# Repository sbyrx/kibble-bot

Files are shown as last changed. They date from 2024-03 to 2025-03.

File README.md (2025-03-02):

# KibbleBot
A 3D printed kibble/treat dispenser powered by an Arduino Nano ESP32 or a Raspberry Pi Pico W. Give your pet a treat even if you're not home!

**Update 2025-03-01:**
Added Arduino support and instructions for controlling KibbleBot via Arduino Cloud.

**Update 2024-04-10:**
Added a new version of the model which allows KibbleBot to be mounted to a wall and the hopper is now attached more securely using screws.

## Features
- Kibbles dispensed through the push of a button or remotely through a web app (Pi Pico) or Arduino Cloud (Nano ESP32)
- Easy to print and build
- Minimal electronics
- Happy puppers

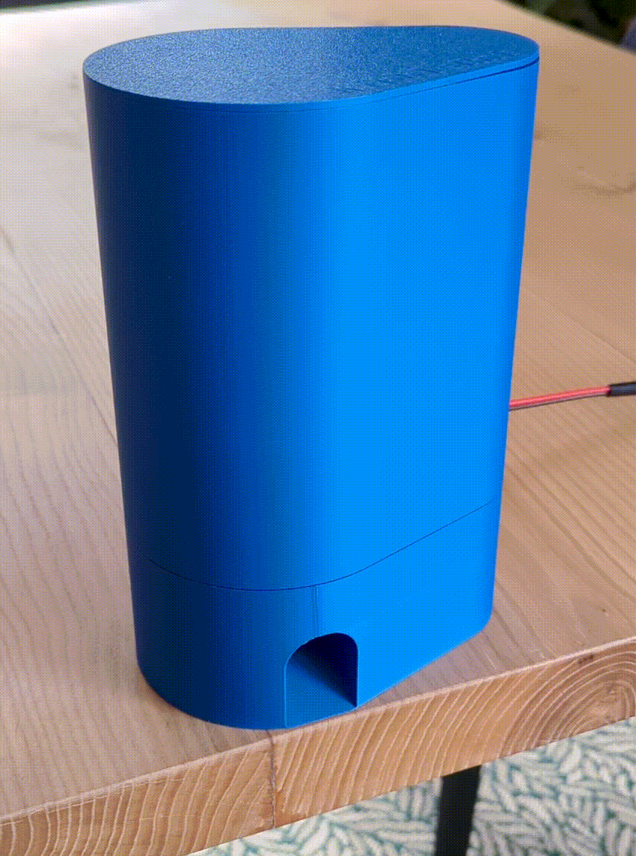
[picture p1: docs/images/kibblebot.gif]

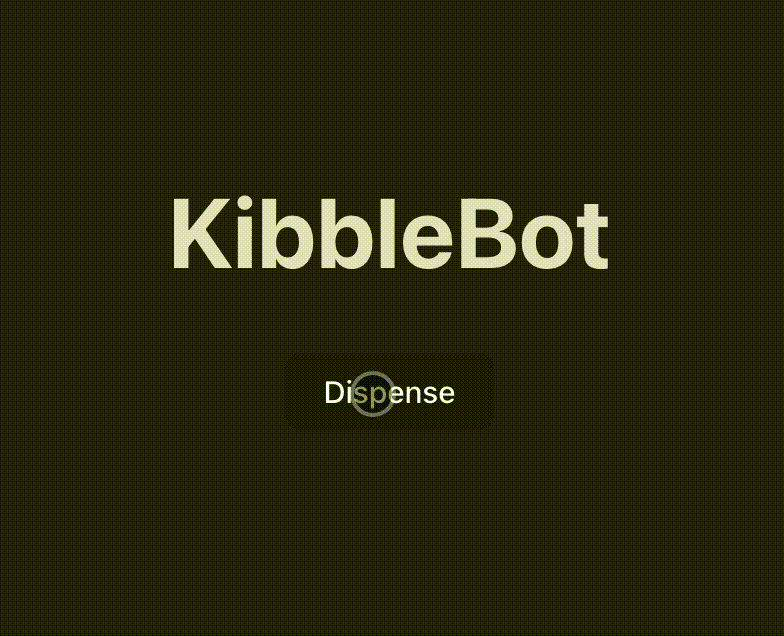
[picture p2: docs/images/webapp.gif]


## Build Instructions
### Parts List
Before you get started, here are all the things you'll need to buy to build your very own KibbleBot. For reference I've included links to the products I purchased:
1. [Arduino Nano ESP 32](https://store.arduino.cc/products/nano-esp32)
1. OR Raspberry Pi Pico W
    - Source from your local [Raspberry Pi authorized reseller](https://www.raspberrypi.com/resellers/)
1. [Easy Driver Stepper Motor Controller](https://ca.robotshop.com/products/easydriver-stepper-motor-controller-a3967)
1. [NEMA 17 Stepper Motor (12V and 350mA)](https://www.pishop.ca/product/stepper-motor-nema-17-size-200-stepsrev-12v-350ma/)
1. 12V Power Supply (I use one I had laying around)
1. [M2x5mm Screws](https://www.amazon.ca/dp/B0C38YFL3D)
1. [M3x6mm Screws](https://www.amazon.ca/dp/B0C38YFL3D)
1. [M3 Flat Washer](https://www.amazon.ca/dp/B0C38YFL3D)
1. [M2x4mm Heat Set Nuts (3.2mm outer diameter)](https://www.amazon.ca/dp/B0CNRSJ1B2)
1. [M3x4mm Heat Set Nuts (4.2mm outer diameter)](https://www.amazon.ca/dp/B0CNRSJ1B2)
1. [6x6x4.3mm TACT Switch Push Button](https://www.amazon.ca/dp/B06Y6DDG8K)
1. [12V DC Barrel Connector (11mm outer diameter)](https://www.amazon.ca/dp/B08SJM2G52)
1. Solder and wire
1. Heat shrink tube
1. [Heat sinks](https://www.amazon.ca/dp/B0814V66JV) (optional, but the Easy Driver can get pretty hot)

### 3D Printed Parts
Print all parts with 0.2mm layer height and 15% infill. I recommend printing both gears with 4 wall loops for some added strength.

I've included [Bambu Studio Project file](docs/models/kibble_bot.3mf) with all parts laid out on two build plates and configured.

|Model|Image|Details|
|-----|-----|---|
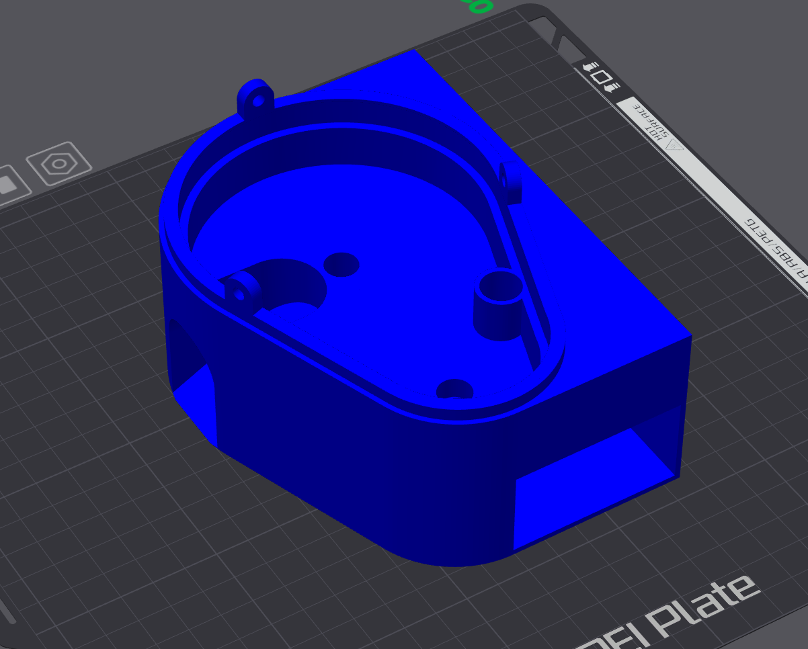
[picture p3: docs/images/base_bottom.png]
Rendering of the Base Bottom
|[Base Bottom](docs/models/base_bottom.stl)||Base of the KibbleBot which the Base Top and Hopper rest on. It has two holes for each gear to rest in and a third for running the stepper motor wire through. It also contains the chute that kibbles come out of and the cut out for the electronics drawer on the side. Can be wall mounted using the holes on the back.<br><br>**Print Orientation**: Right side up<br>**Quantity**: 1<br>**Supports**: Yes|
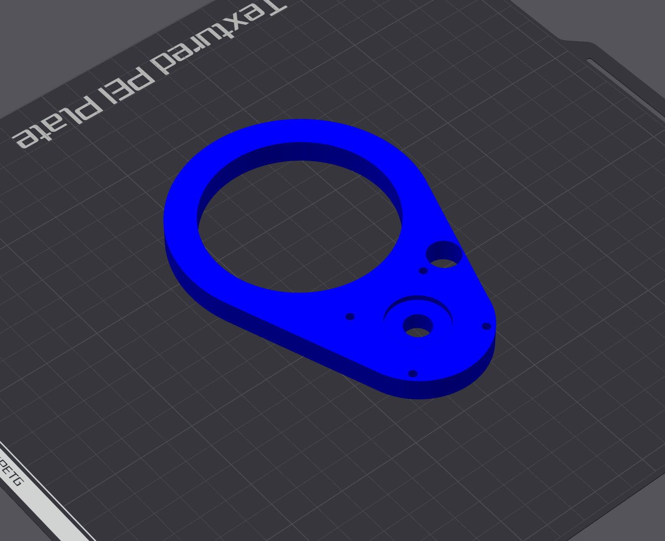
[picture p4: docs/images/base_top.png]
Rendering of the Base Top
|[Base Top](docs/models/base_top.stl)||The Base Top sits inside the Base Bottom covering both gears. It has mounting holes in a 31mm pattern to mount the NEMA 17 stepper motor. You may need to drill out the holes with a small drill bit in order to fit the screws in.<br><br>**Print Orientation**: Side up down<br>**Quantity**: 1<br>**Supports**: No|
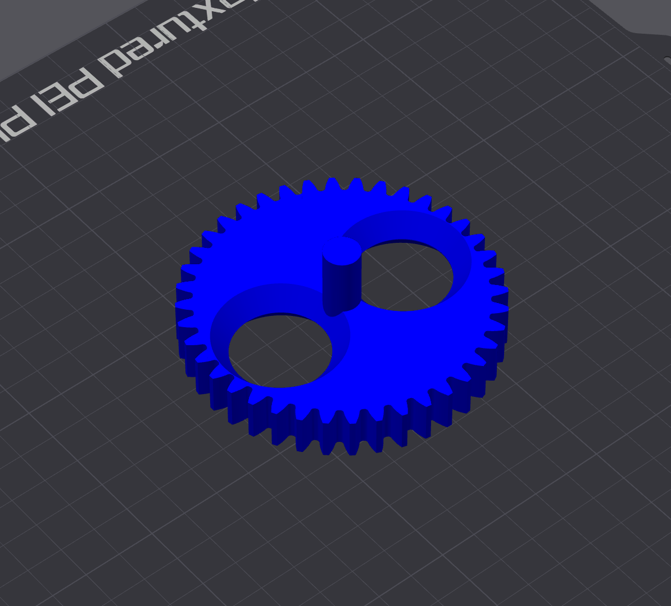
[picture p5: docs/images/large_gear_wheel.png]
Rendering of the Large Gear Wheel
|[Large Gear Wheel](docs/models/large_gear_wheel.stl)||The Large Gear Wheel is spun 180 degrees by the Small Gear Wheel allowing kibbles to fall through it and down the chute in the base bottom. It also has two holes for the optional Stir Sticks if you find that kibbles are getting stuck in the Hopper.<br><br>**Print Orientation**: Side up down<br>**Quantity**: 1<br>**Supports**: No|
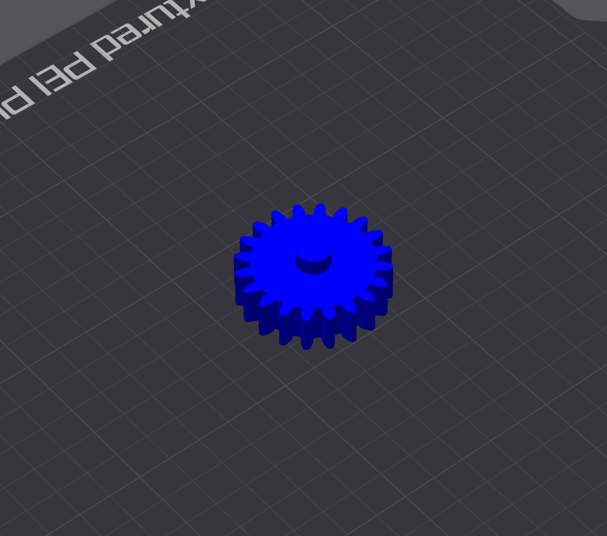
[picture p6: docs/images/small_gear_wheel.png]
Rendering of the Small Gear Wheel
|[Small Gear Wheel](docs/models/small_gear_wheel.stl)||The Small Gear Wheel is connected to the stepper motor and turns the Large Gear Wheel.<br><br>**Print Orientation**: Side up down<br>**Quantity**: 1<br>**Supports**: No|
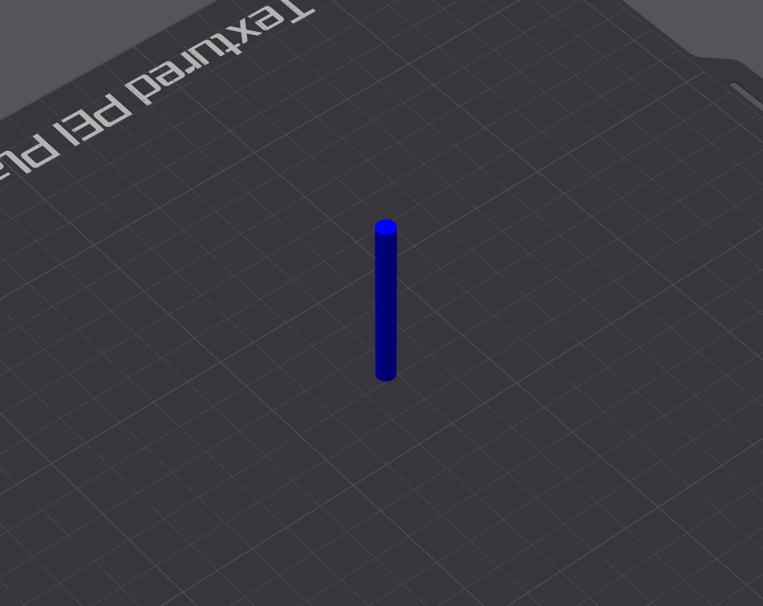
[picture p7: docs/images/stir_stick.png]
Rendering of the Stir Stick
|[Stir Stick](docs/models/stir_stick.stl) (optional)||Slots into the top of the Large Gear Wheel and can help with kibbles getting stuck in the Hopper and not flowing through.<br><br>**Print Orientation**: Vertical<br>**Quantity**: 2<br>**Supports**: Yes (brim)|
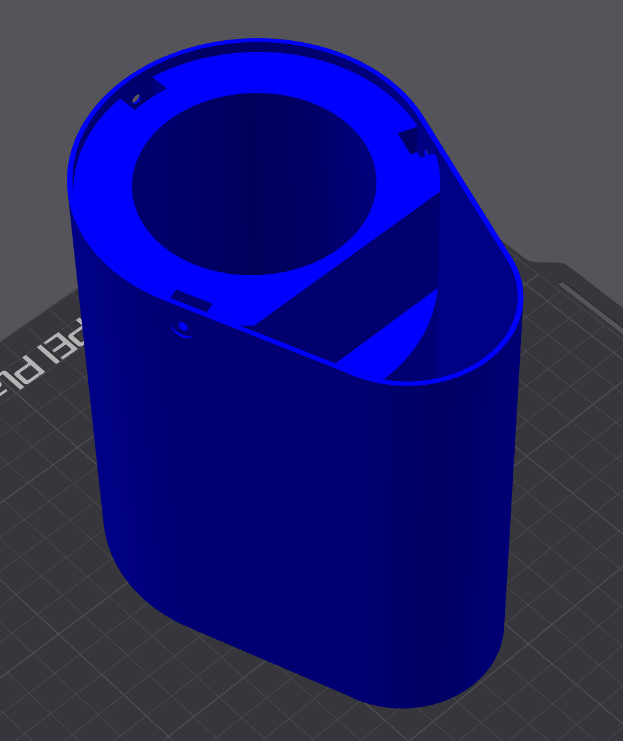
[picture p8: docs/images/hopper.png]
Rendering of the Hopper
|[Hopper](docs/models/hopper.stl)||The Hopper sits on top of the Base Bottom and holds kibbles to be dispensed. Contains a cut out so that it will fit over the stepper motor.<br><br>**Print Orientation**: Up side down<br>**Quantity**: 1<br>**Supports**: No|
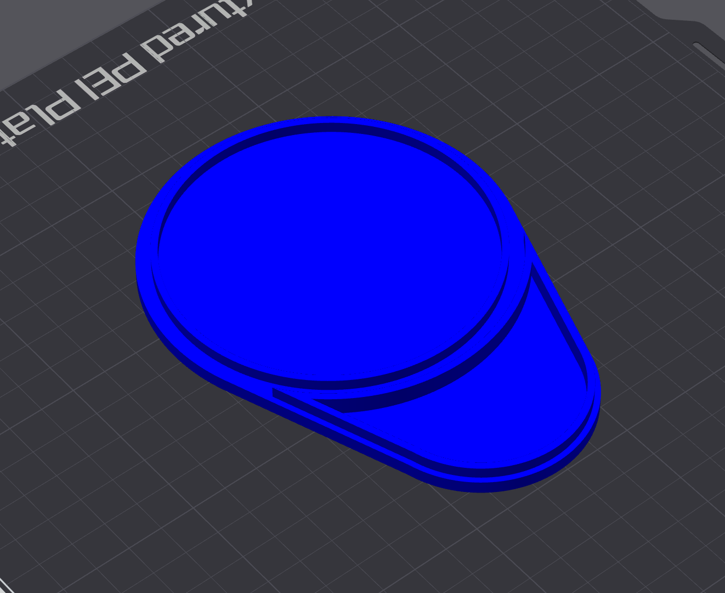
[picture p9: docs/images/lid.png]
Rendering of the Lid
|[Lid](docs/models/lid.stl)||Sits on top of the Hopper to close it off.<br><br>**Print Orientation**: Up side down<br>**Quantity**: 1<br>**Supports**: No|
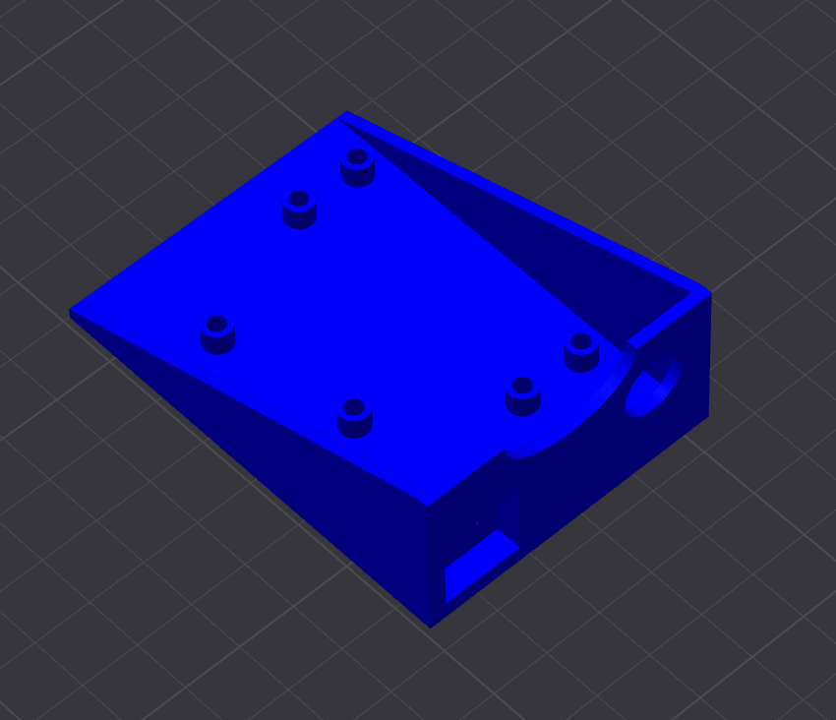
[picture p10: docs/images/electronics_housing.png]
Rendering of the Electronics Housing
|[Electronics Housing](docs/models/electronics_housing.stl)||Houses the Raspberry Pi Pico and the Easy Driver with four holes for the M2 heat set nuts to mount both boards. Also has cut outs for the barrel connector to pass through and to mount the button.<br><br>**Print Orientation**: Right side up<br>**Quantity**: 1<br>**Supports**: Yes|
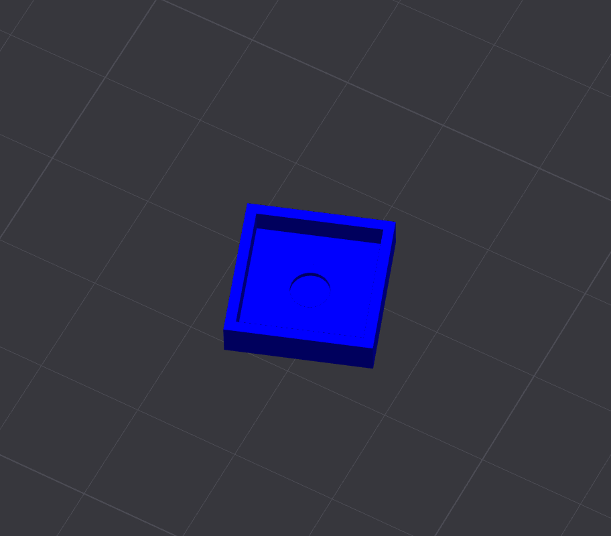
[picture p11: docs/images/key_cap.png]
Rendering of the Key Cap
|[Key Cap](docs/models/key_cap.stl)||The Key Cap is glued on top of the TACT Button and fits inside of a recessed compartment in the Electronics Housing.<br><br>**Print Orientation**: Up side down<br>**Quantity**: 1<br>**Supports**: No|
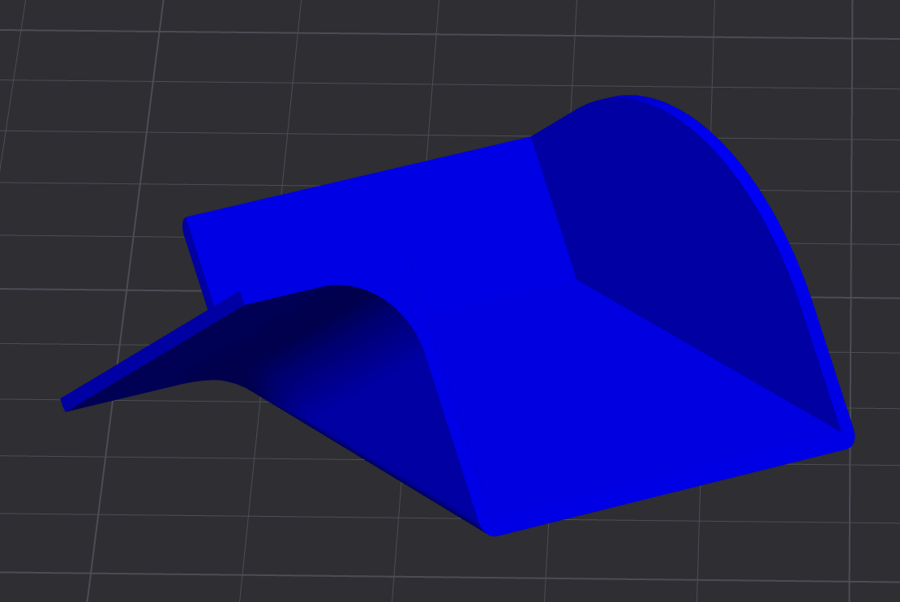
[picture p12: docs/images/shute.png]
Rendering of the Shute
|[Shute (optional)](docs/models/shute.stl)||Redirects the kibbles off to the left instead of straight down.<br><br>**Print Orientation**: Flat side<br>**Quantity**: 1<br>**Supports**: Yes|

### Assembly
Begin by setting the M3 heat set nuts into the three tabs in the Base Bottom which will hold the hopper in place.

Mount the stepper motor to the Base Top. Pass the ribbon cable through the holes in the Base Top and Base Bottom into the electronics drawer.

Then, assemble the rest of the 3D printed parts like so:

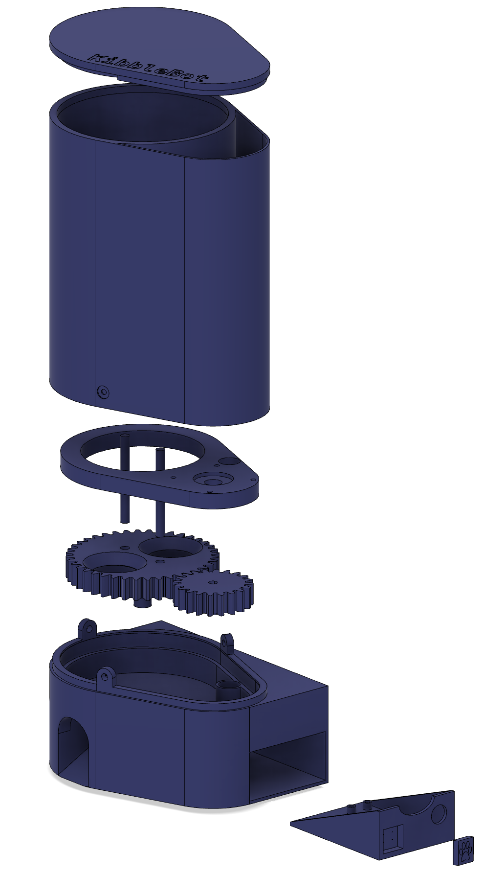
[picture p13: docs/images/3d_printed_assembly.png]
KibbleBot Exploded View


Screw three M3x6mm screws with flat washers through the holes in the Hopper to securely attach it to the Base Bottom.

## Electronics
Below I've provided instructions for two different options for adding smarts to your KibbleBot, either an Arduino Nano ESP32 using Arduino Cloud (easy) or an Raspberry Pi Pico W with a simple web server (a bit more complicated).

### Arduino Nano ESP32
#### Wiring
Since the Nano uses 3.3V logic, the first thing you should do is switch the Easy Driver to use 3.3V logic as well by soldering SJ2 closed (placing a small glob of solder on the two pads on the bottom left hand corner of the board where it's written "5V/3V"). You can confirm you've done this correctly by measuring the voltage across the +5V Output and GND, which should now be 3.3V.

Next, wire the Easy Driver to the Nano as follows:
1. DIR -> D2
1. STEP -> D3
1. SLP -> D4
1. GND -> GND

Connect one side of the TACT Button to D5 and the other side to ground. I used a little bit of CA glue on the back of the button to glue it to the electronics housing, as well as some glue on the back of the keycap to glue it to the TACT Button.

The Easy Driver has a 5V (3.3V) output which can be used to power the Nano. Wire the 5V (now 3.3V) output on the Easy Driver to VIN on the Nano and GND to GND. The Nano's VIN pin can accept an input voltage range of 6-21V, so you could also power it directly from the 12V power supply.

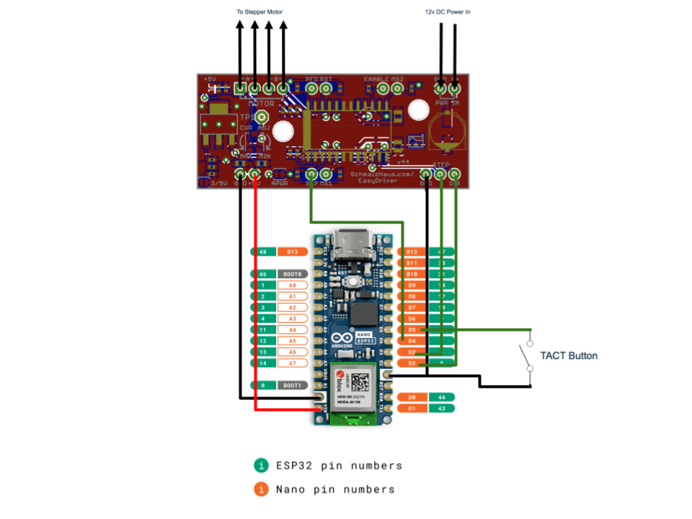
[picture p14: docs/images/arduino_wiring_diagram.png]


Set the heat set nuts into their holes in the bottom of the housing, and mount both boards using the M2 screws.

Plug in your stepper motor, connect your 12V power supply to PWR IN on the Easy Driver, and you should be all set with the electronics!

#### Code
Begin by following [the instructions](https://docs.arduino.cc/tutorials/nano-esp32/cloud-setup/) on the Arduino website for configuring your Nano ESP32, connecting it to your WiFi, and hooking it up to the Arduino Cloud, and creating a new "Thing".

Once completed, on the Setup tab of your Thing, add a new Read/Write variable called `dispense` of type `boolean`. 

Now select the Sketch tab. The Arduino Cloud IDE will have auto-generated a sketch with some boilerplate code for connecting to WiFi and to the cloud as well as a function called `onDispenseChange()` which will be triggered anytime our `boolean` variable is changed.

Open up `kibblebot.ino` and copy the contents of it into your sketch in the Arduino Cloud. Compile the sketch and upload it to the Nano.

The last step is to create a [Dashboard](https://app.arduino.cc/dashboards) which will tell the Nano to dispense kibbles when a button is pressed. Create a new Dashboard, click the Edit button, then Add, and choose the Button type. Link it to your `dispense` variable and give it a name.

When the button is pressed, `onDispenseChange()` will be called in your sketch via the Arduino Cloud, and kibbles will be dispensed!

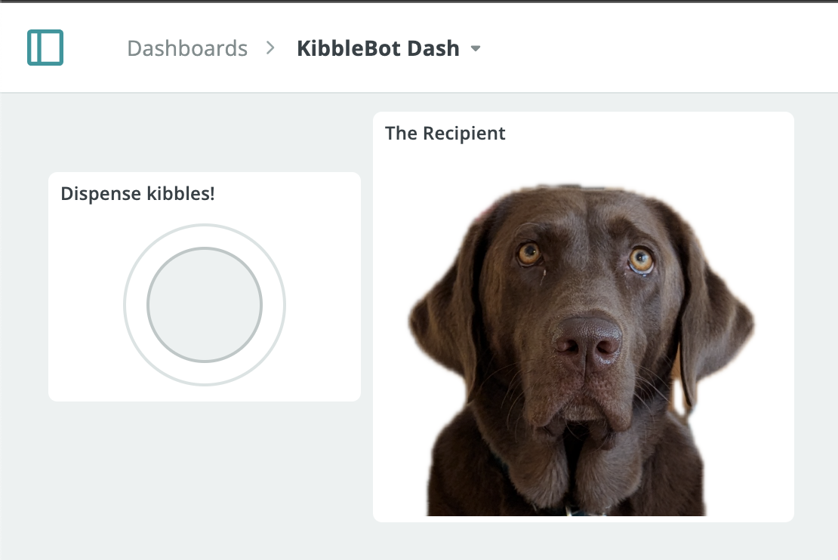
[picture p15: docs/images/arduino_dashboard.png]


### Raspberry Pi Pico
#### Wiring
Since the Pico uses 3.3V logic, the first thing you should do is switch the Easy Driver to use 3.3V logic as well by soldering SJ2 closed (placing a small glob of solder on the two pads on the bottom left hand corner of the board where it's written "5V/3V"). You can confirm you've done this correctly by measuring the voltage across the +5V Output and GND, which should now be 3.3V.

Next, wire the Easy Driver to the Pico as follows:
1. DIR -> GP15
1. STEP -> GP14
1. GND -> GND (Pin 18)
1. SLP -> GP13 

Connect one side of the TACT Button to GP10 and the other to ground (Pin 13). I used a little bit of CA glue on the back of the button to glue it to the electronics housing, as well as some glue on the back of the keycap to glue it to the TACT Button.
+
The Easy Driver has a 5V (3.3V) output which I'm taking advantage of to power the Pico. Wire the 5V (now 3.3V) output on the Easy Driver to VSYS on the Pico, and GND to GND.

Set the heat set nuts into their holes in the bottom of the housing, and mount both boards using the M2 screws.

Plug in your stepper motor, connect your 12V power supply to PWR IN on the Easy Driver, and you should be all set with the electronics!

**Note:** I've opted to solder headers to each board and make the connections using jumper wires. That being said, it's important to make sure the PWR IN and stepper motor connections are solid or you risk blowing up the Easy Driver. Always power off the Easy Driver before plugging/unplugging the stepper motor!

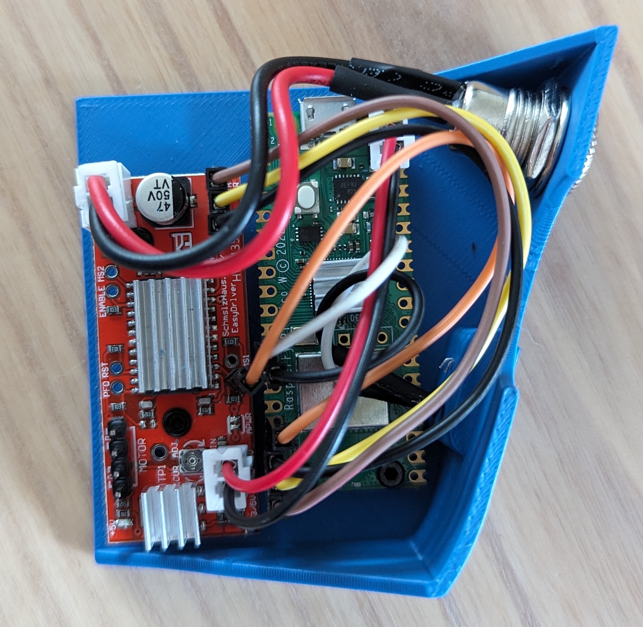
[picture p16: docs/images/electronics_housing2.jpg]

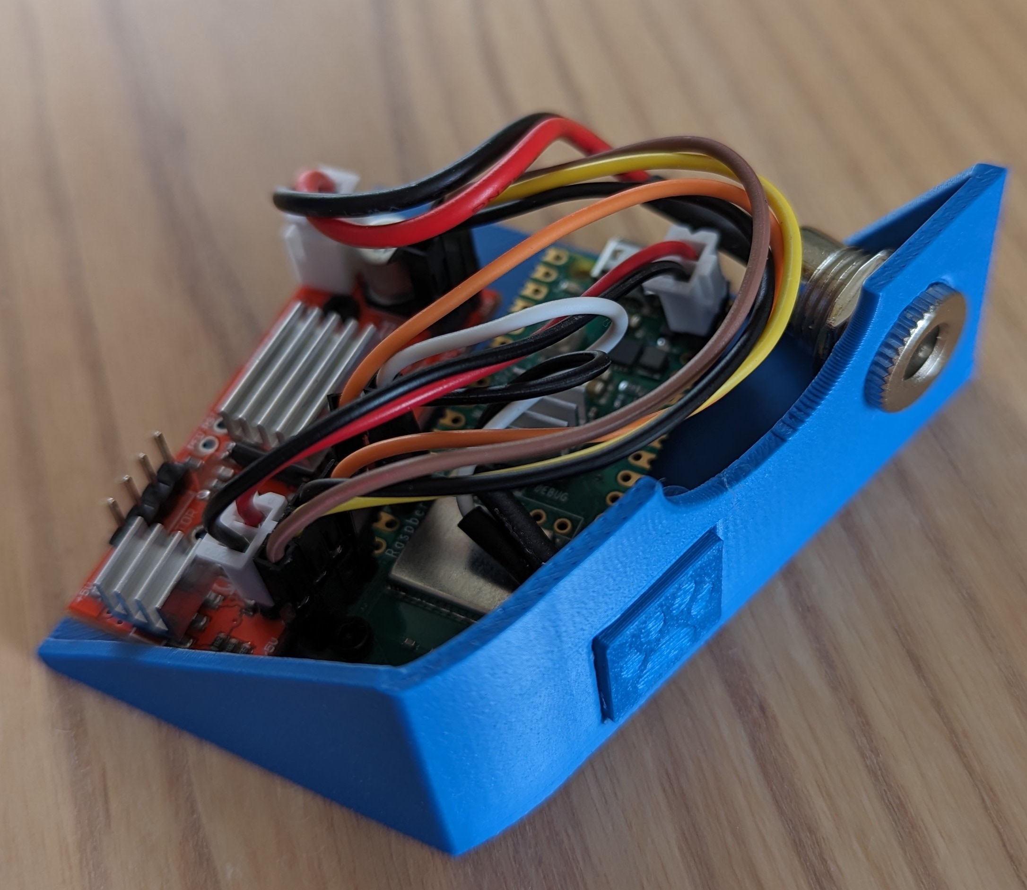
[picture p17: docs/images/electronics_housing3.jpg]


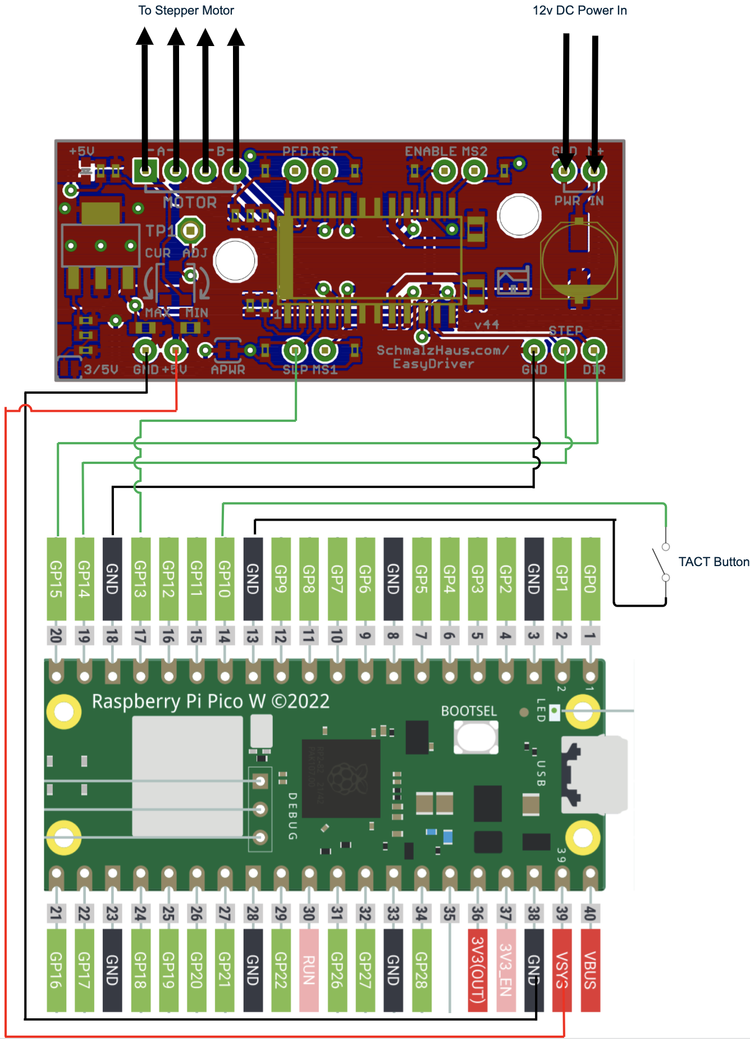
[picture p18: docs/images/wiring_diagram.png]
KibbleBot wiring diagram


#### Code

The KibbleBot software for the Pico is written in Micropython. Follow the [instructions here](https://www.raspberrypi.com/documentation/microcontrollers/micropython.html) to flash Micropython onto your board.

I also recommend setting up a Visual Studio project and installing the [MicroPico extension](https://github.com/paulober/MicroPico) to copy the code to the board.

You'll also need to have `NodeJS` and `npm` set up on your machine in order to build the web app.

##### main.py

This is the Micropython code which runs on the Pico and interfaces with the Easy Driver to turn the stepper motor and dispense kibbles. It first connects to WiFi and then listens for button presses and has a simple web server to listen for web requests.

To run the code on your Pico, first edit `main.py` and set the WiFi SSID and password. Then connect your Pico to your computer, and wait for VSCode to show "Pico Connected" in the bottom toolbar. Then right click on `main.py` and click "Upload current file to Pico".

##### Web App

I've created a simple Svelte app which `main.py` serves up and allows kibbles to be dispensed from a web browser. The web app is built into a single HTML file to make it easy for the Micropython code to serve up.

You'll need to build the web application and copy the resulting `index.html` to the Pico:
1. Open up a terminal and set the working directory to `/web`
1. Run `npm install`
1. Run `npm run build`
1. Open the resulting `/web/dist/index.html` file
1. Right click on it and click "Upload current file to Pico"

In VSCode, click "Toggle Pico-W-FS" in the bottom toolbar. The "Pico (W) Remote Workspace" view should now show two files: `main.py` and `index.html`.

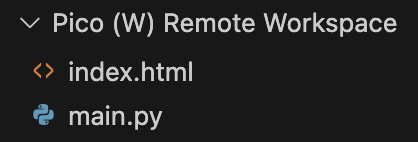
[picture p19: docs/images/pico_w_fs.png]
Screenshot of the Pico W FS view


With both files copied to your Pico, you're good to go! Unplug it from your computer and power everything up with the 12V supply. When the Pico shows a solid green LED it means it's connected to WiFi and ready to go. Navigate to the Pico's IP address in your browser and click "Dispense"!

#### Accessing KibbleBot remotely

If your home router supports running a VPN server, this is likely your easiest option for accessing the KibbleBot when not at home. Simply connect your phone/laptop to the VPN and browse to the local IP address of the Pico.

Another option is a [Cloudflare Zero-Trust tunnel](https://www.cloudflare.com/products/tunnel/), but this requires you to run the Cloudflare client on another machine that's always powered on.

In my set up I've opted to use a Cloudflare tunnel as I already have the Cloudflare client running on my home server and several tunnels configured. This set up enables me to share the URL with friends and family so they can dispense kibbles too. I've included the Micropython code that I use (`main_rate_limiting.py`) which keeps track of the number of kibbles each user has dispensed and limits them to once per week.

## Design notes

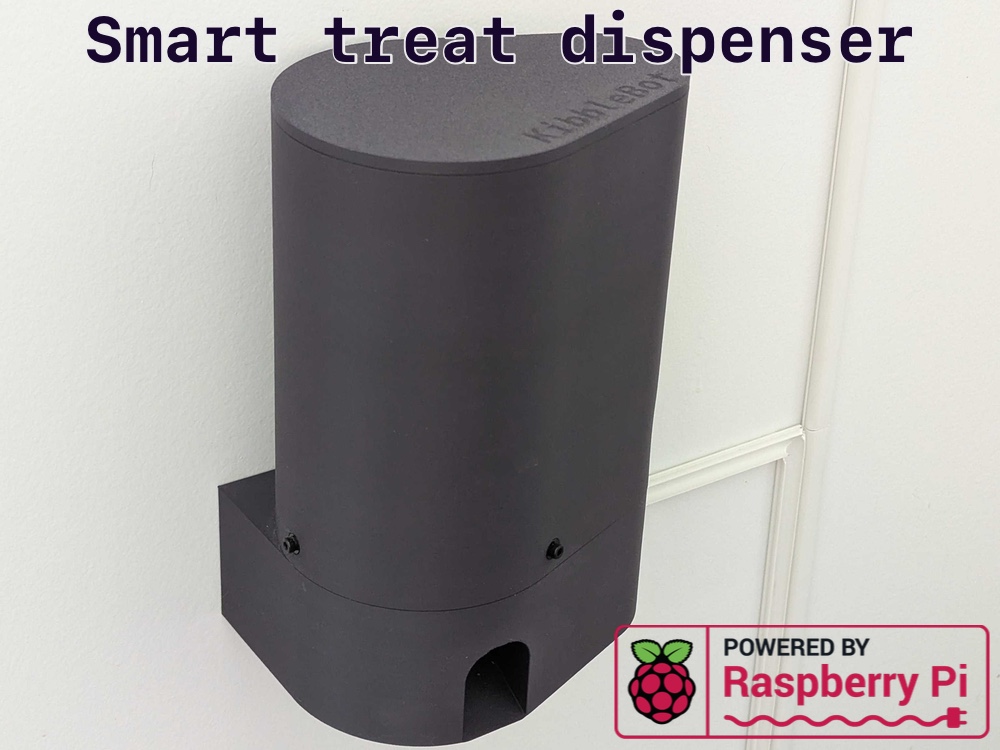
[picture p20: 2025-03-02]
docs/images/thumbnail-pico.jpeg

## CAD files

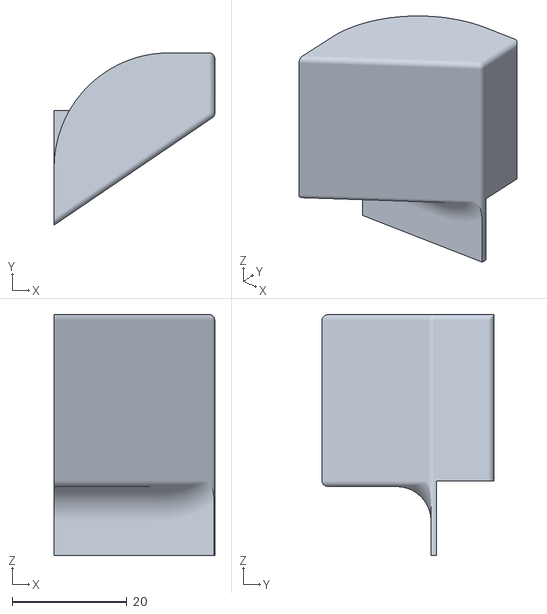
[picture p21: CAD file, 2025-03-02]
docs/models/shute.stl
28.0 x 30.0 x 42.0

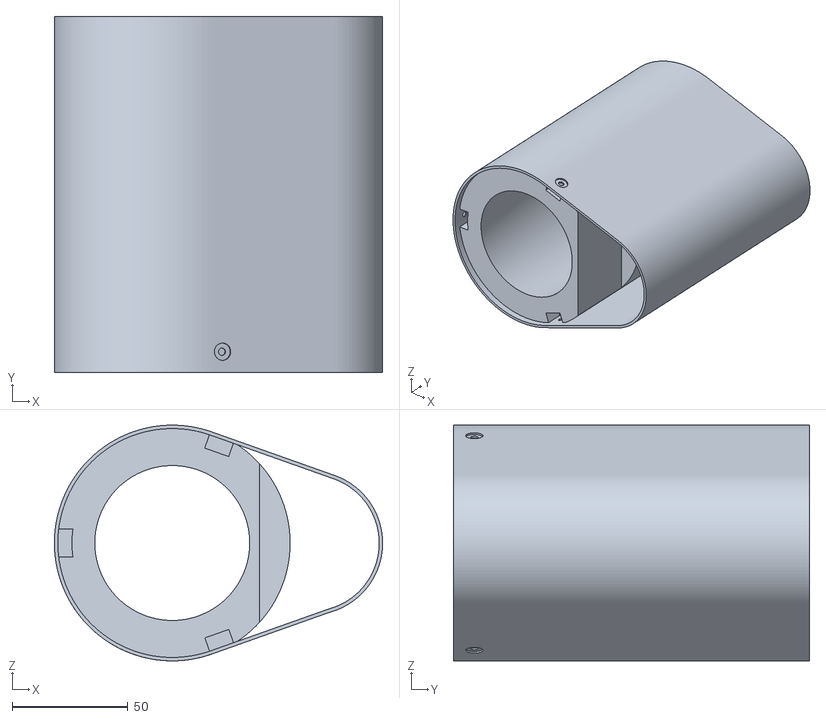
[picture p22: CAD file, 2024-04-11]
docs/models/hopper.stl
142.0 x 154.0 x 102.0

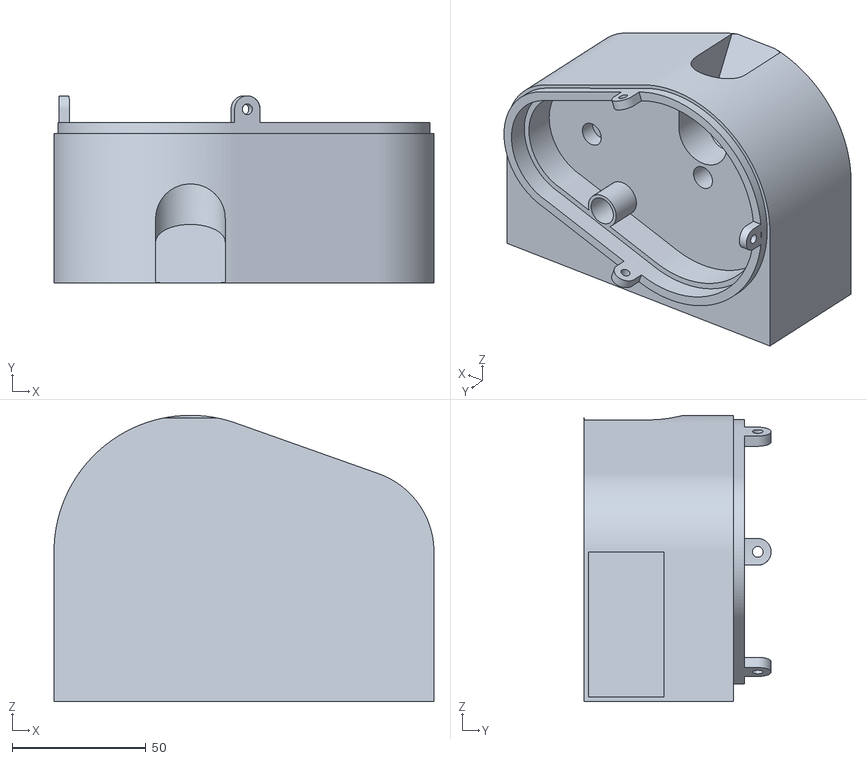
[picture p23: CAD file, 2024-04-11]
docs/models/base_bottom.stl
142.0 x 70.0 x 107.0

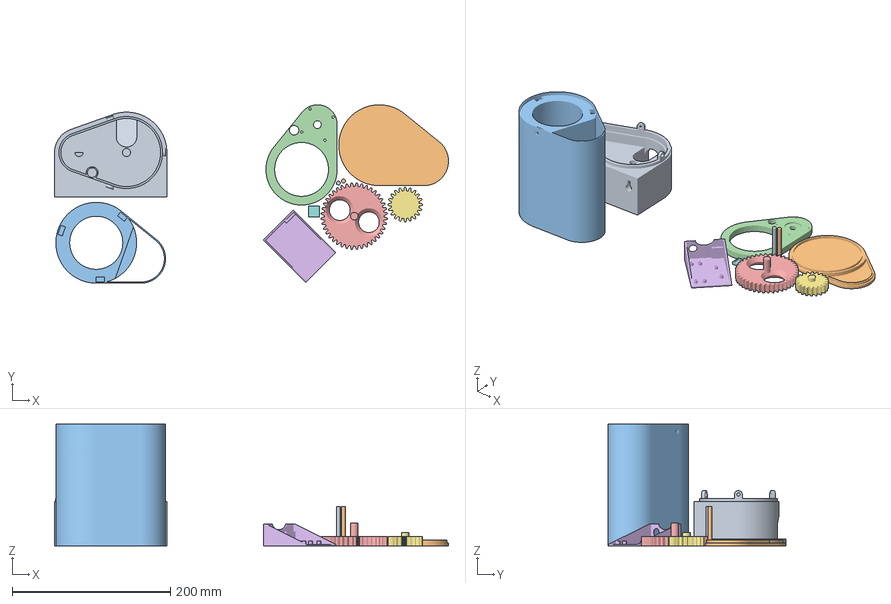
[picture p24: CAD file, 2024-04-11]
docs/models/kibble_bot.3mf
497.6 x 225.2 x 154.0 mm
base_bottom.stl
lid.stl
hopper.stl
base_top.stl
large_gear_wheel.stl
electronics_housing.stl
small_gear_wheel.stl
key_cap.stl
stir_stick.stl x 2

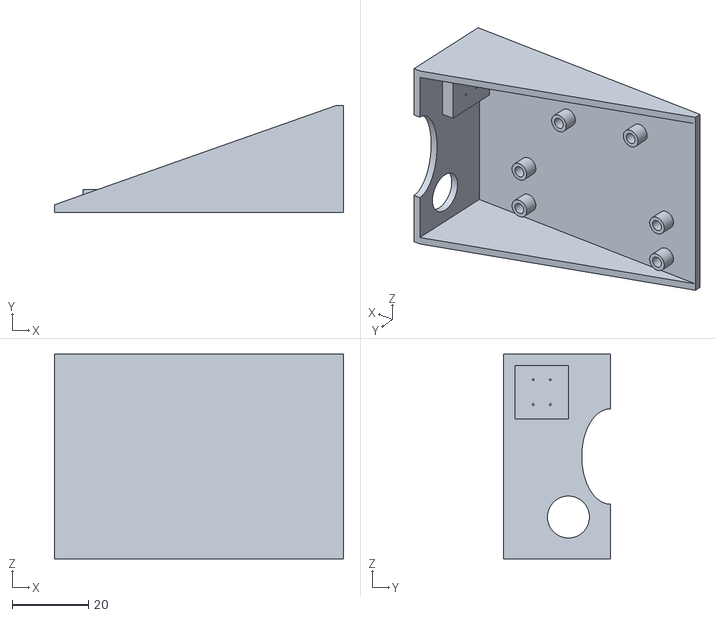
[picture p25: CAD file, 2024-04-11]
docs/models/electronics_housing.stl
75.8 x 28.0 x 53.7

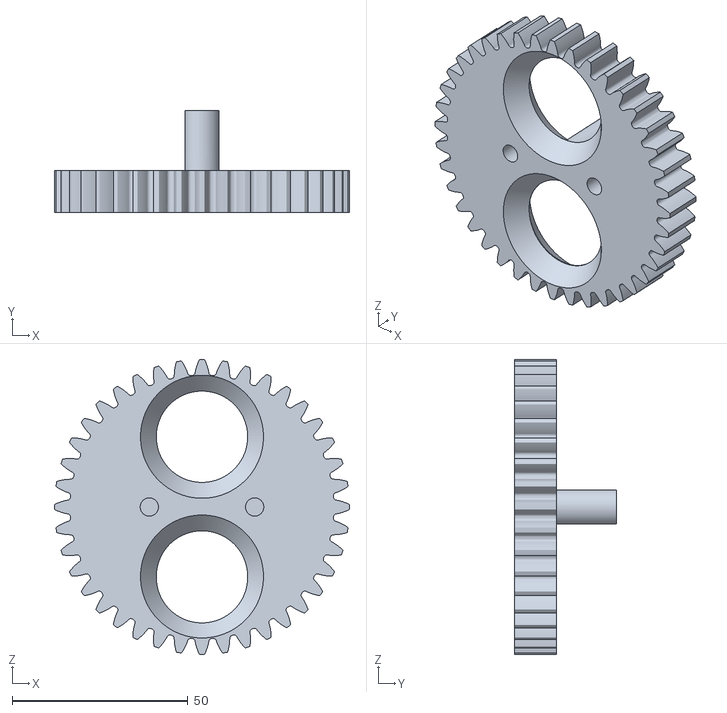
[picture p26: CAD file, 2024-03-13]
docs/models/large_gear_wheel.stl
84.0 x 29.0 x 84.0

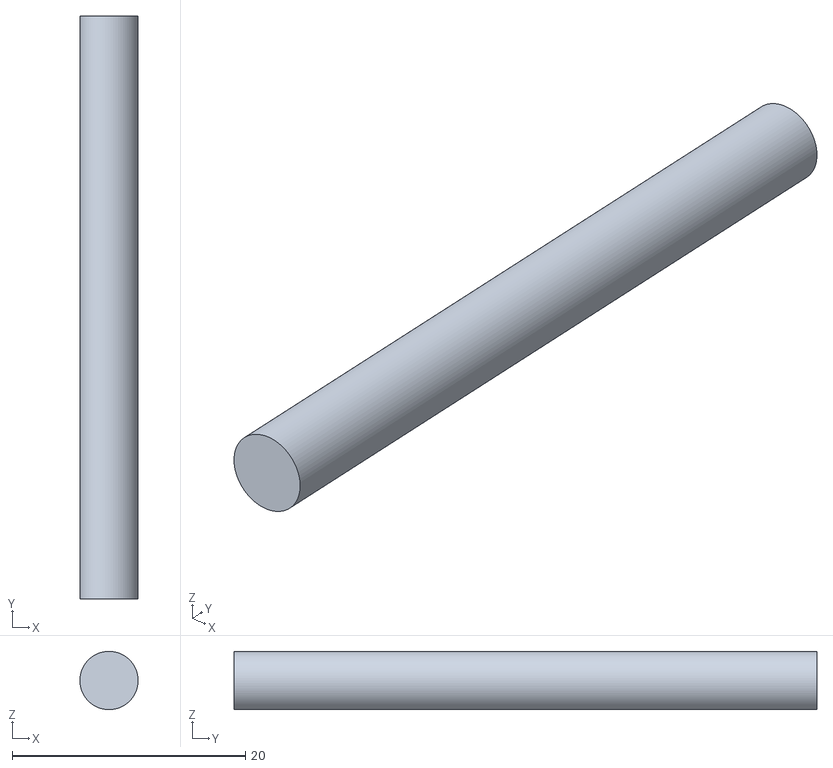
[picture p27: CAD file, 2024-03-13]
docs/models/stir_stick.stl
5.00 x 50.0 x 4.99

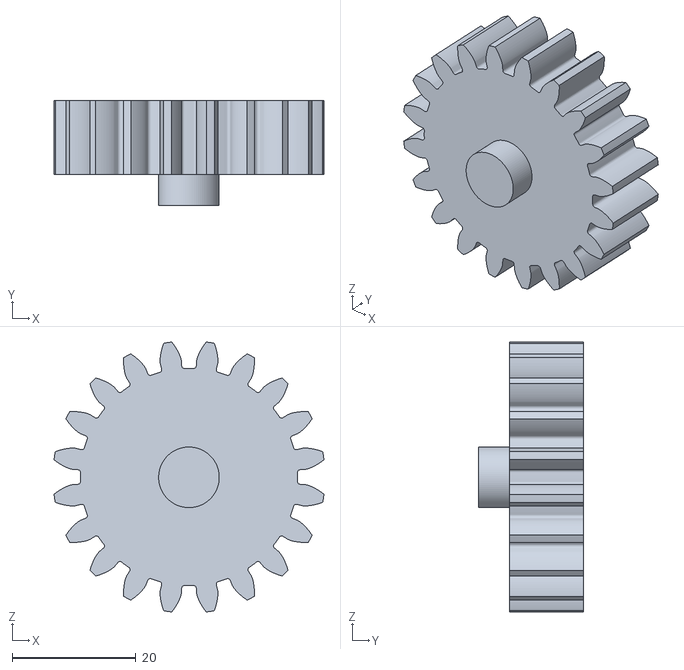
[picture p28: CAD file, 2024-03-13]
docs/models/small_gear_wheel.stl
43.6 x 17.0 x 43.6

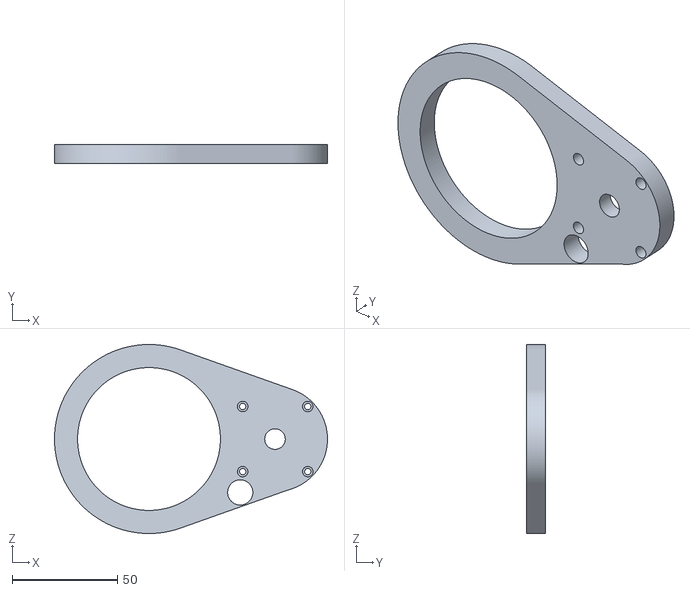
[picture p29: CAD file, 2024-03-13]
docs/models/base_top.stl
130.0 x 9.00 x 90.0

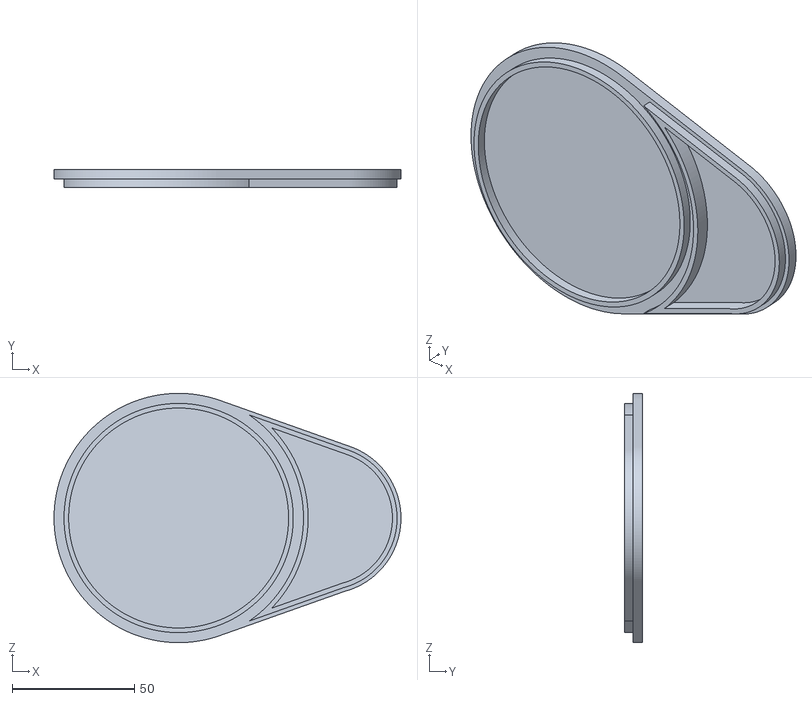
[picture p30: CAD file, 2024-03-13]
docs/models/lid.stl
142.0 x 7.50 x 102.0

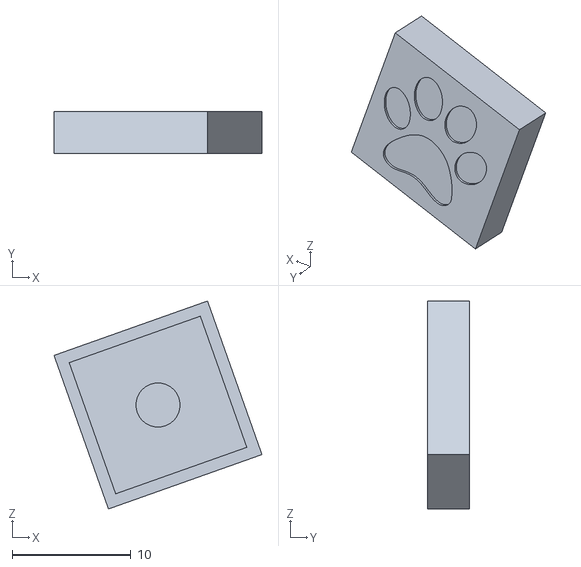
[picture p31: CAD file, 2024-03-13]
docs/models/key_cap.stl
17.5 x 3.50 x 17.5

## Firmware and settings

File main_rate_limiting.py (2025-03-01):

# This version of main.py is designed to sit behind a CloudFlare Zero-Trust tunnel
# and keep track of how many kibbles each authenticated user has dispensed. It limits 
# the number of kibbles a user can dispense to one per week. The idea is to be able
# to open up access to the KibbleBot to friends and family.

import network
import socket
import time
import select
import ure
import json
import ntptime

from machine import Pin

led = Pin('LED', Pin.OUT)
dir = Pin(15, Pin.OUT)
step = Pin(14, Pin.OUT)
sleep = Pin(13, Pin.OUT)
button = Pin(10, Pin.IN, Pin.PULL_UP)

led.low()
sleep.low()
dir.low()
step.low()

ssid = 'SSID'
password = 'PASSWORD'

database = dict()

# These users are not limited to once per week and can dispense unlimited kibbles
allowlist = ['myemail@domain.com']

# Connect Pi to WiFi
def connectWifi():
    wlan = network.WLAN(network.STA_IF)
    wlan.active(True)
    wlan.connect(ssid, password)

    max_wait = 10
    while max_wait > 0:
        if wlan.status() < 0 or wlan.status() >= 3:
            break
        max_wait -= 1
        print('connecting to wifi...')
        time.sleep(1)

    if wlan.status() != 3:
        raise RuntimeError('network connection failed')
    else:
        print('connected')
        status = wlan.ifconfig()
        print('ip = ' + status[0])
        ntptime.settime()
        print('current time is ' + str(time.localtime()))


 # Listen for HTTP requests
def handleWebRequest():
    addr = socket.getaddrinfo('0.0.0.0', 80)[0][-1]
    cl = socket.socket()
    s = socket.socket()
    s.bind(addr)
    s.listen(1)

    print('listening on', addr)
    led.high()

    while True:
        try:
            poller = select.poll()
            poller.register(s, select.POLLIN)
            res = poller.poll(100)

            if res:
                cl, addr = s.accept()
                print('client connected from', addr)
                request = ''

                cl_file = cl.makefile('rwb', 0)
                while True:
                    line = cl_file.readline()
                    request = request + str(line)
                    if not line or line == b'\r\n':
                        break

                url = ure.search(r'GET (/\S*) HTTP', request)
                email = ure.search(r'Cf-Access-Authenticated-User-Email: (\S*)\\r\\n', request)

                if url and email:
                    servePage(cl, url.group(1), email.group(1))
                else:
                    cl.send('HTTP/1.0 400 Bad Request\r\n\r\n')
                
                cl.close()
            
            # In between waiting for web requests, check if the dispense button has been pressed
            if button.value() == 0:
                print('button pressed')
                dispense()

        except OSError as e:
            cl.close()
            s.close()
            print('connection closed')

def dispense():
    print('dispensing kibble')
    sleep.high()
    for x in range(1600):
        step.value(1)
        time.sleep_us(250)
        step.value(0)
        time.sleep_us(250)
        if x % 100 == 0:
            led.toggle()
    led.high()
    sleep.low()
    print('kibble dispensed')

def loadDatabase():
    databaseFile = open('database.json', 'r')
    database = json.loads(databaseFile.read())
    databaseFile.close()
    return database


def saveDatabase():
    databaseFile = open('database.json', 'w')
    databaseFile.write(json.dumps(database))
    databaseFile.flush()
    databaseFile.close()

def canDispense(email):
    if email not in database:
        database[email] = 0

    if email in allowlist:
        database[email] = database[email] + 1
        return True;

    year, month, mday, hour, minute, second, weekday, yearday = time.localtime()
    weekNumber = yearday/7

    if database[email] <= weekNumber:
        database[email] = database[email] + 1
        return True
    return False

def servePage(cl, url, email):
    if url == '/dispense':
        if canDispense(email):
            dispense()
            saveDatabase()
            print(email + ' dispensed kibble #' + str(database[email]))
            cl.send('HTTP/1.0 200 OK\r\nContent-type: application/json\r\n\r\n{"status":"Kibbles dispensed!", "kibblesDispensed":"' + str(database[email]) + '"}')
        else:
            cl.send('HTTP/1.0 200 OK\r\nContent-type: application/json\r\n\r\n{"status":"You have no more kibbles left to give!", "kibblesDispensed":"' + str(database[email]) + '"}')
    elif url == '/':
        page = open('index.html', 'r')
        
        cl.send('HTTP/1.0 200 OK\r\nContent-type: text/html\r\n\r\n')
        for line in page.read():
            cl.send(line)

        page.close()
    elif url == '/stats' and email in allowlist:
        cl.send('HTTP/1.0 200 OK\r\nContent-type: application/json\r\n\r\n' + json.dumps(database))
    else:
        cl.send('HTTP/1.0 404 Not Found\r\n\r\n')

database = loadDatabase()
connectWifi()
handleWebRequest()

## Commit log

2024-03-13 Fixed a bug with sleep
    The sleep pin was no longer being pulled low on the Easy Driver after dispensing
    [main.py, main_noauth.py]
2024-03-13 Added a README, models and images
    [base_bottom.stl, base_top.stl, electronics_housing.stl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]
2024-04-11 Adding version 2 of model
    Base bottom can now be wall mounted
    Hopper is attached to base bottom with screws
    [base_bottom.stl, electronics_housing.stl, hopper.stl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]
2025-03-01 Added support for Arduino, other fixes and upgrades
    [main_rate_limiting.py]
2025-03-02 Added Arduino wiring diagram and shute
    [shute.stl]
